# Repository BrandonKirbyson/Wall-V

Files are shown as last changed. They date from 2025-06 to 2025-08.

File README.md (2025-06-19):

# Wall-V (Wheeled and Legged Locomotion Vehicle)

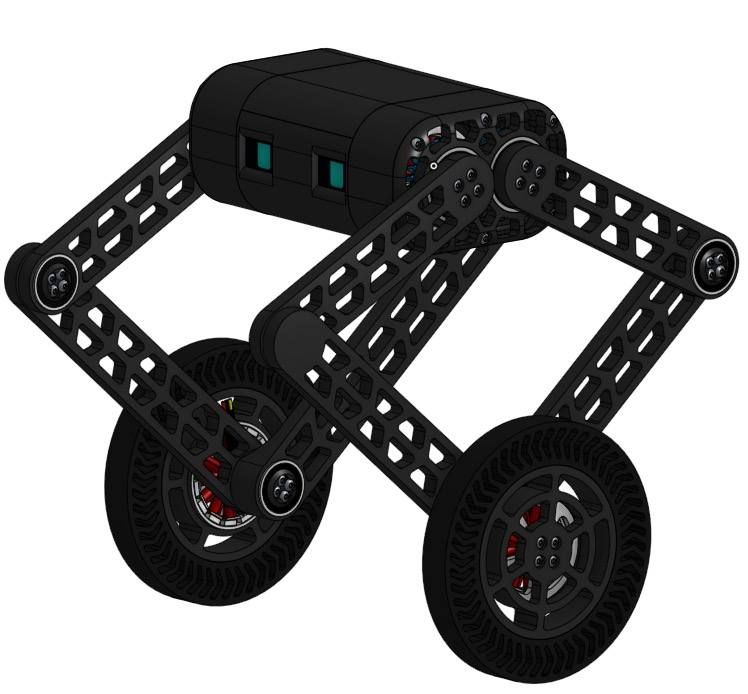
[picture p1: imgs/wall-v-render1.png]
Wall-V Render


Wall-V is a 2 legged, self-balancing robot that has wheels and can jump. It is designed to be able to go up hills and have uneven height on each side. The robot uses an ESP-Wroom-32 as a fast microcontroller to stay balanced. We are planning to use either PID to maintain balance.

## Why we are building this

We are building Wall-V to experiment with self-balacing robots that have the capability to jump. Jumping will allow to robot to go over small obstacles and be more manuverable and it will have to have high torque motors to align the robot.

So far throughout the building process, the hardest thing has been creating the leg design that allows the robot to jump. We have thought about many different designs but concluded that putting a ball bearing as the joint will still allow the robot to jump while not requiring an extra motor to move. The legs are both attached to each other and 1 motor will provide the torque to lift both legs at once. Additionally, the wheels are not linked so they can be at independent heights.

## Wiring Diagram

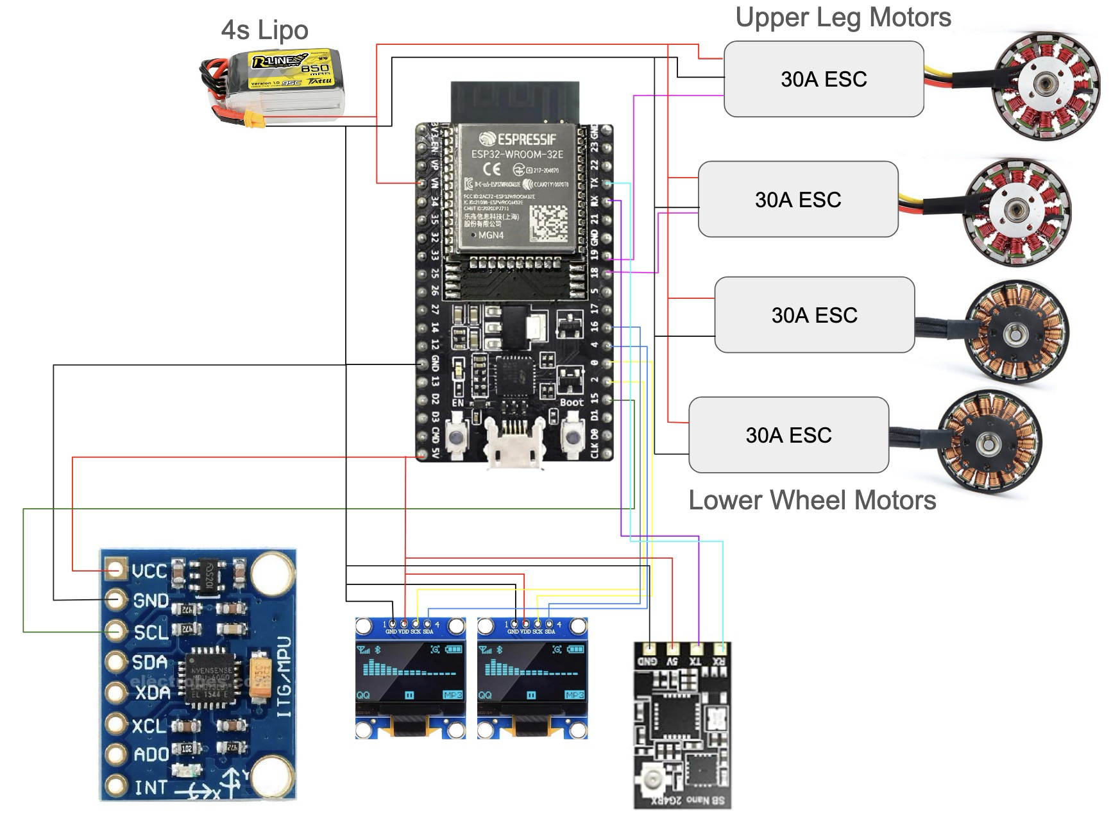
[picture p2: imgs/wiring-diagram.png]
Wiring Diagram


## Parts List

Subtotal Cost of Parts on Amazon: $123.9 (does not include tax and shipping)

Subtotal Cost of Parts on AliExpress: $34.89 (does not include tax and shipping)

Subtotal Cost of Parts: $158.79 (does not include tax and shipping)

Total Cost of Parts: $175.92 (includes tax and shipping)

Extra Spent on Amazon: $27.12 (extra we will cover for faster shipping, not spent using HCB funds)

| Quantity | Name | Notes | Amazon Link | Ali Link | Amazon Price | Aliexpress Price | Ordering From | Ordered |
| --- | --- | --- | --- | --- | --- | --- | --- | --- |
| 4 | VGEBY Brushless Motor 1PCS 5010 360KV | These two motors power the arms and have high torque that can quickly pull up the legs enabling the robot to jump | https://a.co/d/61lIr4G | https://www.aliexpress.us/item/2251832668557589.html | 27.62 | 15.10 | Aliexpress | 2/4 |
| 1 | WWZMDiB 4Pcs AS5600 Magnetic Encoder 3.3V 12bit high Precision Magnetic Induction Angle Measurement Sensor Module | These are used for getting motor position | https://a.co/d/6U3z8iJ | https://www.aliexpress.us/item/3256802834839452.html | 10.99 | 5.67 | Amazon | No |
| 1 | ESP32-DevKitC-32E Development Board | This is the main microcontroller for the robot which has a very fast tick rate for self-balancing | https://a.co/d/bIcHKEl | https://www.aliexpress.us/item/3256804290552594.html | 11 | 2.46 | Aliexpress | No |
| 4 | ZMR 40A Bidirectional Brushless 2-6S UBEC 3A 5V ESC | These ESCs will control the leg and wheel motors | https://a.co/d/9KbKRcA | https://www.aliexpress.us/item/2255800049335968.html | 14.99 | 11.89 | Amazon | No |
| 1 | MF148ZZ Flanged Ball Bearing ID 8mm x OD 14mm x Width 4mm | Smaller flanged bearings to support leg pivots | https://a.co/d/eTWzlf1 | https://www.aliexpress.us/item/3256807921303726.html | 8.99 | 5.49 | Amazon | No |
| 2 | F6802-2RS 10PCS Flanged Bearing 15×24×5mm | Medium size flanged bearings for the leg joints at knee and wheel | https://a.co/d/7eKafdc | (not cheaper) | 9.99 | - | Amazon | No |
| 1 | F6804-2RS 4PCS Flanged Ball Bearing 20mm x 32mm x 7mm | Larger flanged bearings for main leg pivot joints in the body | https://a.co/d/40CGgTH | (not cheaper) | 8.99 | - | Amazon | No |
| 1 | SpeedyBee ELRS FPV Receiver - 2.4ghz ExpressLRS Nano Receiver Drone RX Module with 78mm UFL T Antenna | ELRS receiver to control the robot with a remote | https://a.co/d/2ItnyXH | https://www.aliexpress.us/item/3256809002280211.html | 14.99 | 12.88 | Amazon | No |
| 1 | 0.96 Inch OLED Display Module 12864 LCD Screen 128x64 IIC I2C OLED Board SSD1315 | 2 small OLED screens that will serve as the robots eyes | https://a.co/d/b7wErMp | https://www.aliexpress.us/item/3256804169233174.html | 9.99 | 2.23 | Aliexpress | No |

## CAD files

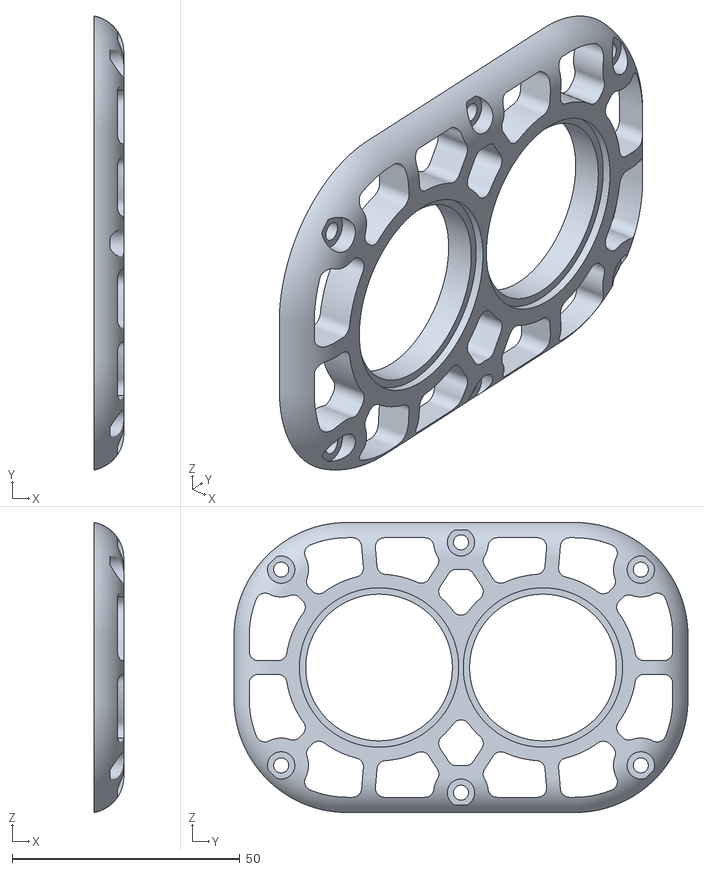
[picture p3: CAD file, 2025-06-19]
models/Leg Motor Cover.stl
6.50 x 99.7 x 63.7

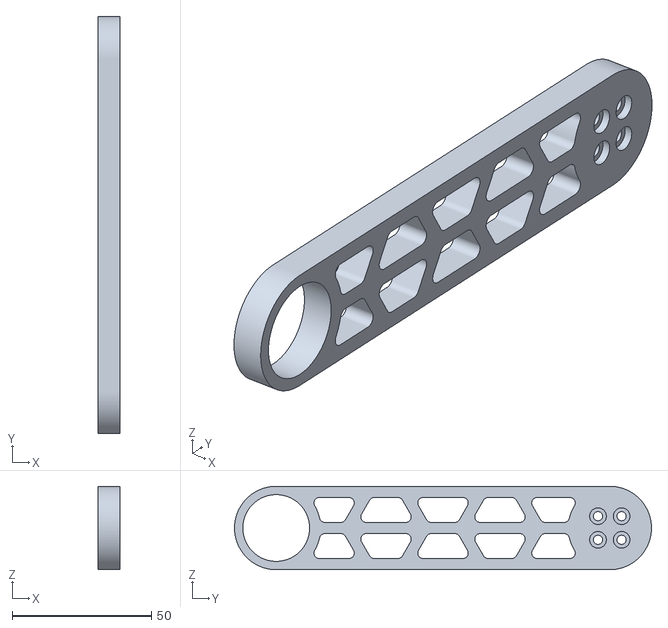
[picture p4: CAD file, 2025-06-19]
models/Front Upper Leg.stl
8.00 x 150.0 x 30.0

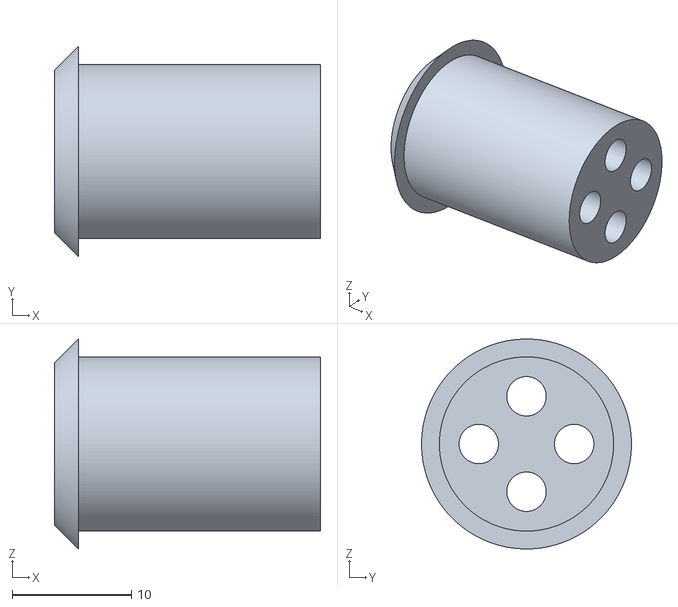
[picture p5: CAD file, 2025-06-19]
models/Wheel Joint Hub.stl
22.3 x 17.6 x 17.6

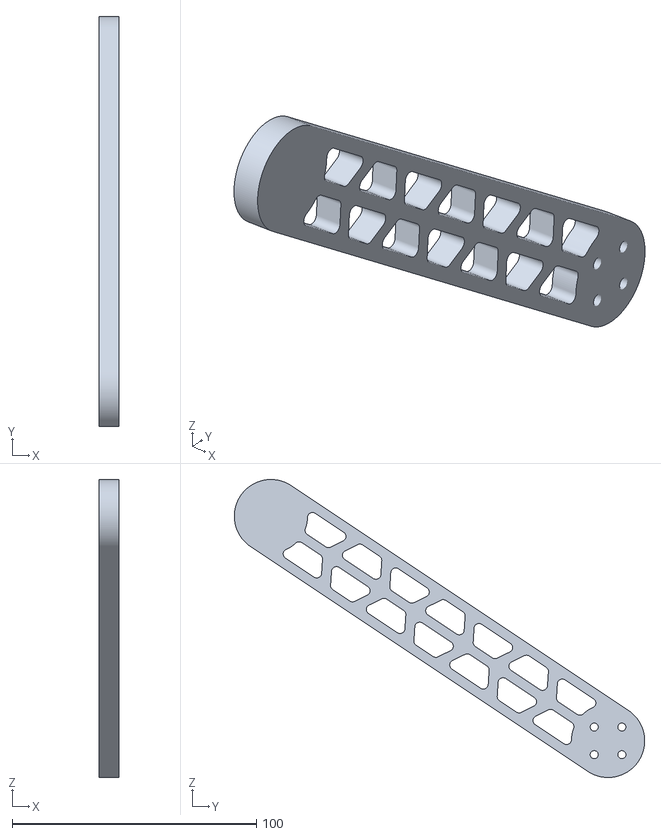
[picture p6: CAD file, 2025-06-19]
models/Front Lower Leg.stl
8.00 x 168.0 x 122.0

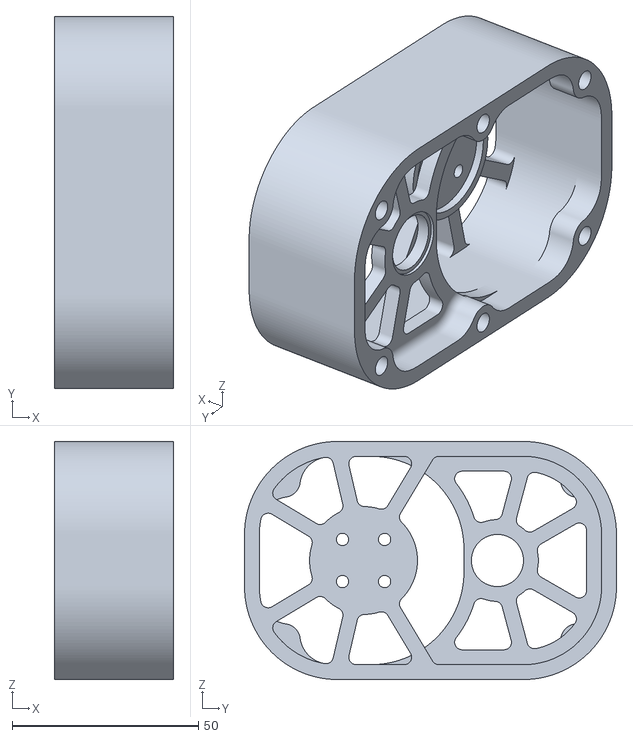
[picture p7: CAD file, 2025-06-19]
models/Right Motor Box.stl
32.0 x 100.0 x 64.0

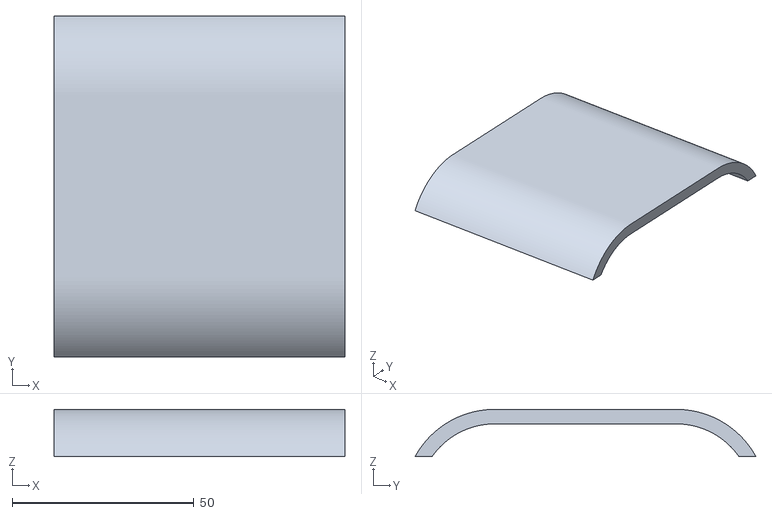
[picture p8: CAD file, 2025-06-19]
models/Upper Body.stl
80.0 x 93.9 x 13.0

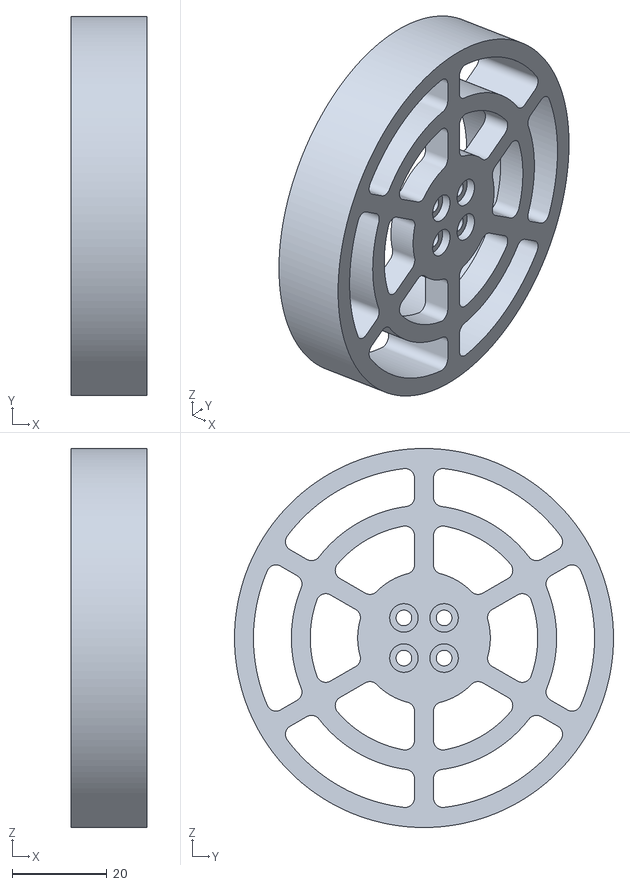
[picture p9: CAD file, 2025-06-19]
models/Wheel Hub.stl
16.0 x 80.0 x 80.0

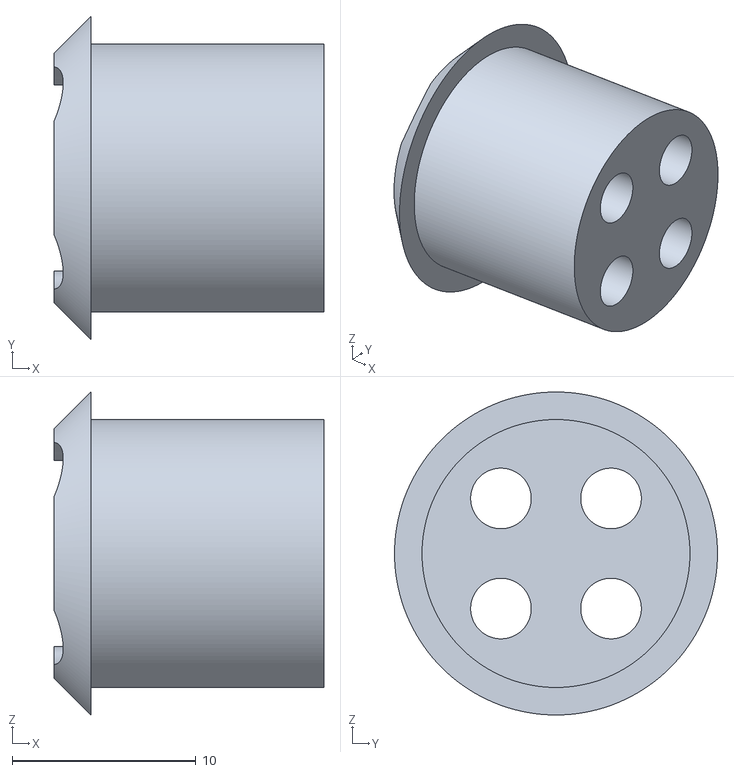
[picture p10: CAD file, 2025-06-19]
models/Knee Hub.stl
14.7 x 17.6 x 17.6

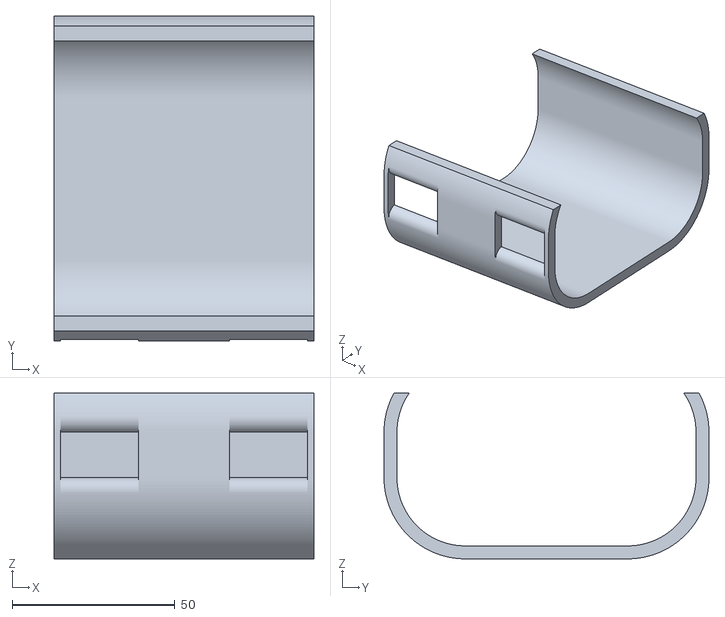
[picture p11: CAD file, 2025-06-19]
models/Lower Body.stl
80.0 x 100.0 x 51.0

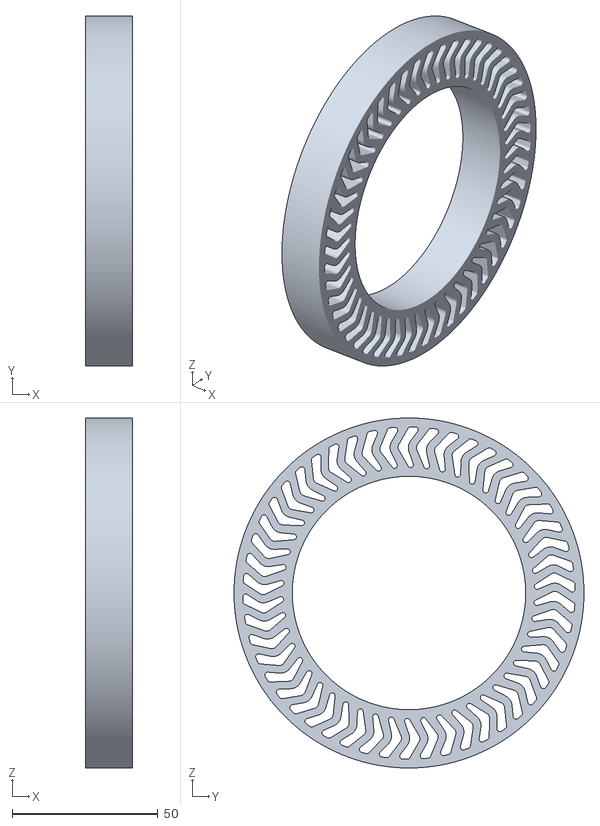
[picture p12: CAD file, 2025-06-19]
models/Tire (TPU).stl
16.0 x 120.0 x 120.0

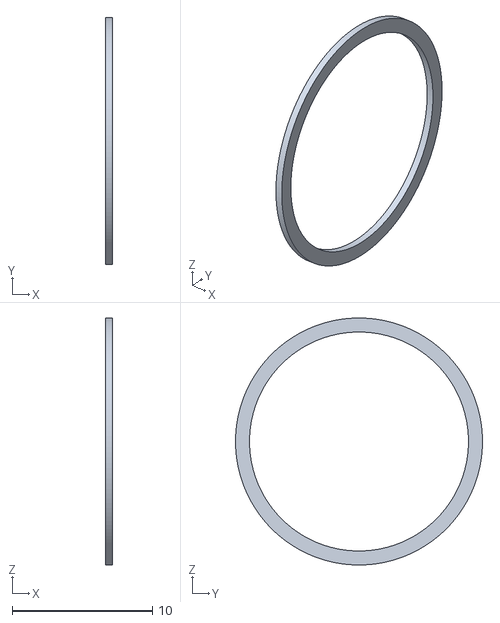
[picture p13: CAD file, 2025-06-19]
models/Knee Spacer.stl
0.5 x 17.6 x 17.6

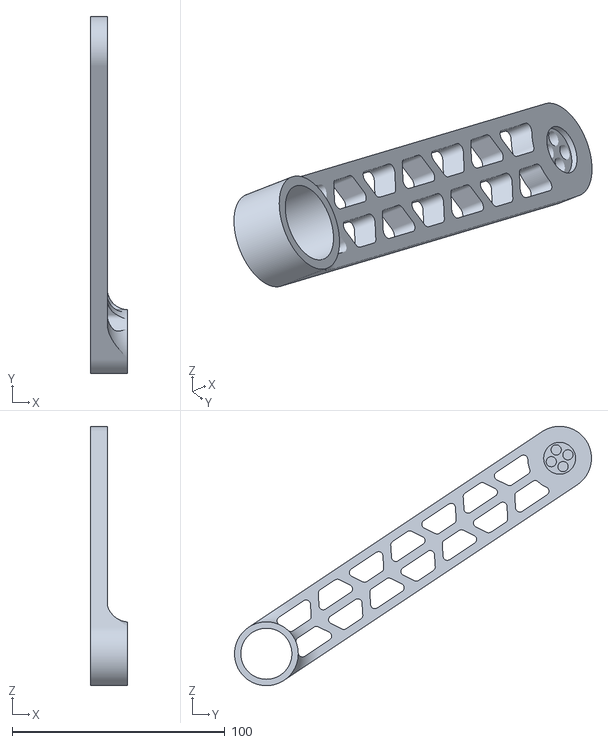
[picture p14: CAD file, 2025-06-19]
models/Back Lower Leg.stl
17.6 x 168.0 x 122.0

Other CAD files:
models/Right Motor Cover.stl
models/Back Upper Leg.stl
models/Leg Motor Box.stl

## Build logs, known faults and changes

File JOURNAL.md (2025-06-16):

---
title: "Wall-V"
author: "Brandon Kirbyson/Tobin Palmer"
description: "Wall-V is a 2 legged, self-balancing robot that has wheels and can jump."
created_at: "2025-06-10"
---

*Note for all time spent, it is counting for 1 person working on the bot, we both worked only worked on it together so the total time is listed here is half the amount for both of us*

## Total Time Spent: 13 Hours

## 6/11/25 - Initial Sketches and First CAD Design

### Time Spent: 2.5 Hours

We started by drawing an initial sketch of the robot's design. It has a motor and gear on each side which allow it to quickly move the wheels up to jump. Additionally, each side is independent so it can go up a hill and have uneven height on each side. We are planning to use an ESP-Wroom-32 as a fast microcontroller so the robot can stay balanced. We are planning to use PID or LQR to balance the robot.
Initial Sketch

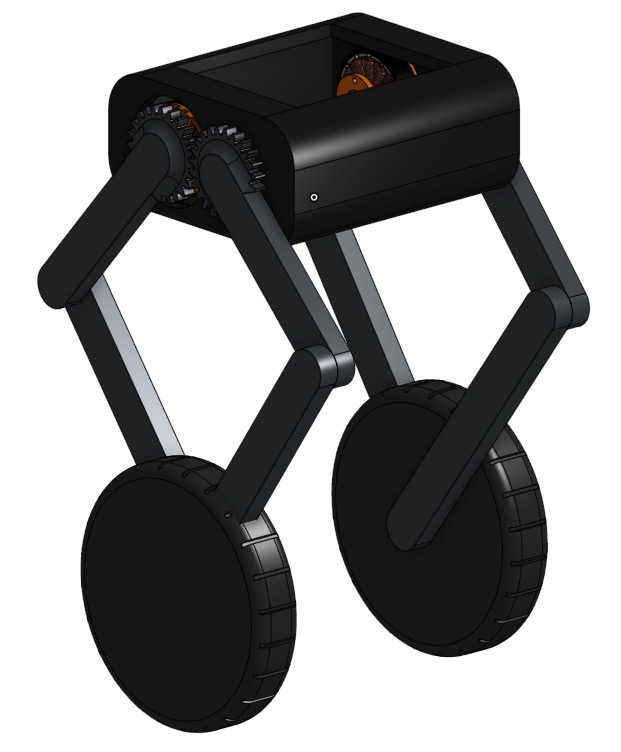
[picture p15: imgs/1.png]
Initial Robot Design


Initial CAD Design of the robot

## 6/12/25 - New CAD Design

### Time Spent: 3.5 Hours

We changed the CAD design to have a mount for the motor and also have the arms be properly mounted with a bearing. Additionally, we changed the style for the motor, now it has a 2 gear design that will ensure the wheels mainly stay centered under the bot.

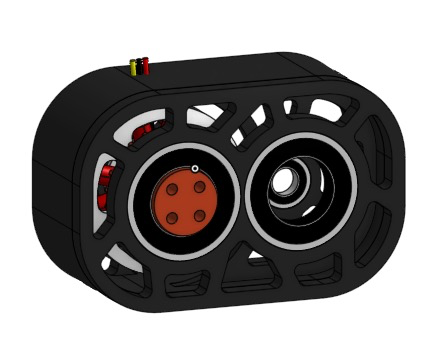
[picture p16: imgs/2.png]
Robot side with motor gears


View of motor without legs attached. Two bearings will help smoothly rotate each leg

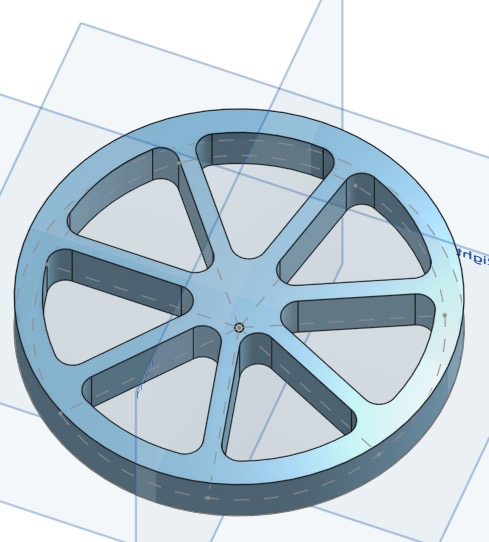
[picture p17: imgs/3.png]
Primative wheel design


Basic wheel which we will wrap rubber to give better traction.

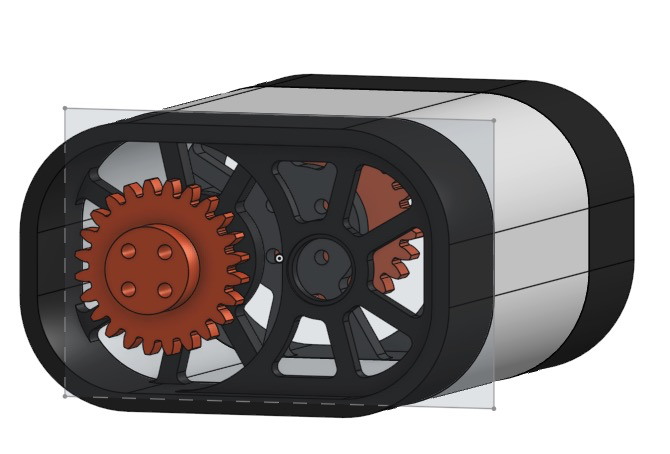
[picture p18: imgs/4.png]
Body of the robot with motors on either side


Joined halfs with empty space for battery, esc and microcontroller.

## 6/13/25 - CAD Design Nearly Finished

### Time Spent: 5 Hours

First picture of testing PID Proof of Concept

Second picture of testing PID Proof of Concept

While designing the model we started to test some old parts we had laying around to see if our IMU would work as fast enough to balance the robot. We used a servo as motor to see kindof what the code would look like, however, in our actual bot we would be using a brushless motor.

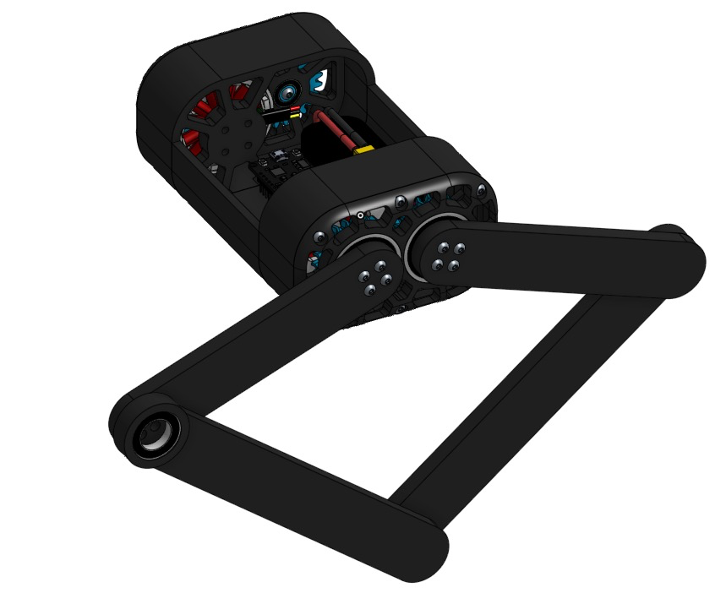
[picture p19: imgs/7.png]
Robot coming along


Picture of the robot with the motors and mounting fully done. We just need to add some mounting for the internal protoboard and fix the legs with proper bearings.

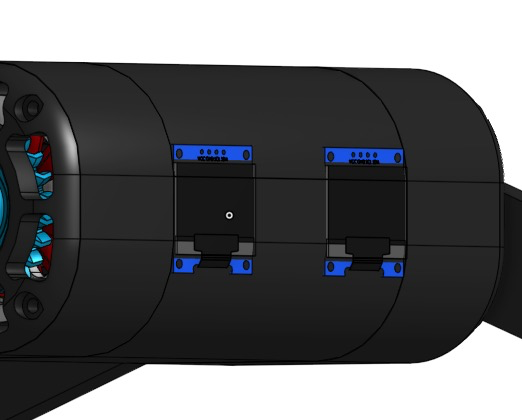
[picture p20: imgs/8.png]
The screens that will serve as eyes


These screens will be used as eyes and will ideally have a animation to might even be dependent on the speed of the robot. We are planning to use the ESP32 to control them.

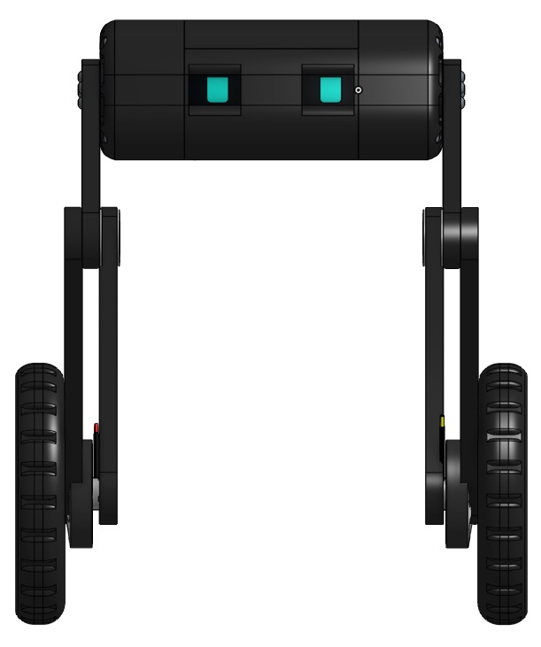
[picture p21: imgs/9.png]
Front view of Wall-V


The front view of the robot shows its design and how the wheels are mounted and an example face of the robot.

The only thing that needs to be improved is the legs and their mounting to the wheels.

## 6/14/25

### Time Spent: 2 Hours

Finished the CAD including making the leg joints work with a bearing and mounting the wheels onto the legs.

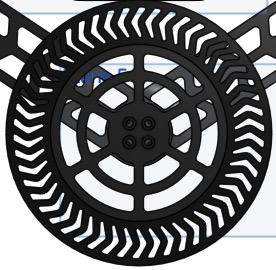
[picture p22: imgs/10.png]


The finished wheel design with a TPU tire to give it more traction. The wheel and leg are both designed to be very light so that the robot can quickly move its legs up and down without using an overly powerful motor.

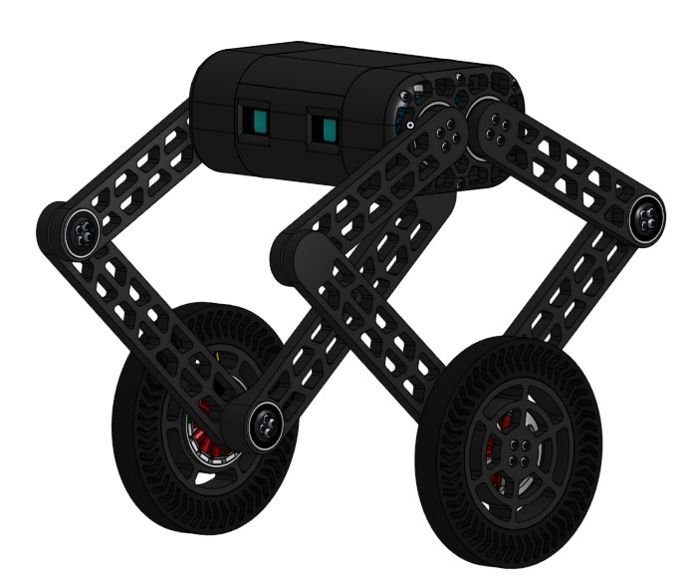
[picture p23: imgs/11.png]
Side view of the robot


The finished robot design

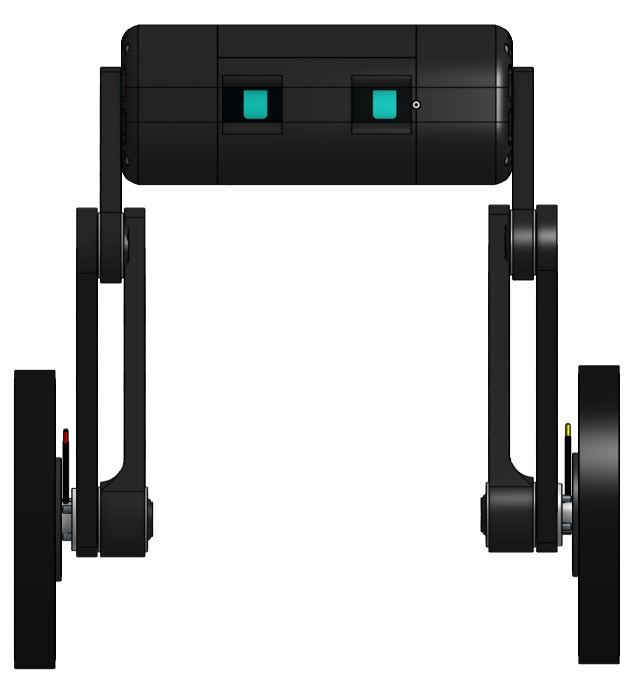
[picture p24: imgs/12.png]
Front view of the robot


Front view of the robot

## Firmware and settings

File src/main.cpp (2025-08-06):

#include <Arduino.h>

void setup()
{
  // Initialize serial communication at 9600 baud rate
  Serial.begin(9600);

  // Wait for the serial port to connect (useful for some boards)
  while (!Serial)
  {
    ; // Wait for serial port to connect. Needed for native USB port only
  }

  Serial.println("Hello, World!");
}

void loop()
{
  // Nothing to do here
  // The setup function already prints "Hello, World!" once
  delay(1000); // Optional: wait for a second before the next iteration
}

// #include <Arduino.h>
// #include <Wire.h>
// // #include <AS5600.h>
// #include <Servo.h>

// const int SW_pin = 2; // digital pin connected to switch output
// const int X_pin = 0;  // analog pin connected to X output
// const int Y_pin = 1;  // analog pin connected to Y output

// // AS5600 as5600;
// Servo esc;

// const int escPin = 12;

// // const float Kp = 0.5;
// // const float Ki = 0;
// // const float Kd = 0.1;
// // // const float Ki = 0.1;
// // // const float Kd = 0.5;

// // double targetAngle = 90.0;
// // double integral = 0.0;
// // double previousError = 0.0;
// // unsigned long lastTime = 0;

// double armExtendedPercent(int rawAngle);
// void setMotorPower(double percent);

// void setup()
// {
//   Serial.begin(9600);
//   Wire.begin();
//   esc.attach(escPin);
//   esc.writeMicroseconds(1000); // arm ESC

//   pinMode(SW_pin, INPUT);
//   digitalWrite(SW_pin, HIGH);

//   delay(2000);

//   // if (as5600.begin())
//   //   Serial.println("AS5600 Working");
//   // else
//   //   Serial.println("AS5600 Not working");

//   // lastTime = millis();
// }
// void loop()
// {
//   int yValue = analogRead(Y_pin);
//   Serial.print(" | Y: ");
//   Serial.println(yValue);

//   // convert Y value from 0-1020 to 0-100
//   double yPercent = (yValue / 1023.0) * 100.0;
//   Serial.print("Y Percent: ");
//   Serial.println(yPercent);

//   // int rawAngle = as5600.readAngle();
//   // double angle = armExtendedPercent(rawAngle);

//   // unsigned long now = millis();
//   // double dt = (now - lastTime) / 1000.0;
//   // lastTime = now;

//   // double error = targetAngle - angle;
//   // integral += error * dt;
//   // double derivative = (error - previousError) / dt;
//   // previousError = error;

//   // double output = Kp * error + Ki * integral + Kd * derivative;

//   // double motorPower = constrain(output, -100.0, 100.0);
//   setMotorPower(yPercent);

//   // // Debug output
//   // Serial.print("Angle: ");
//   // Serial.print(angle);
//   // Serial.print(" | Error: ");
//   // Serial.print(error);
//   // Serial.print(" | Output: ");
//   // Serial.println(output);

//   delay(3);
// }

// double armExtendedPercent(int rawAngle)
// {
//   const double MIN_ANGLE = 214;
//   const double MAX_ANGLE = 123;

//   const double MIN_POSITION = 0;
//   const double MAX_POSITION = 90;

//   double angle = rawAngle * 360.0 / 4096.0;

//   if (angle > MIN_ANGLE)
//     return MIN_POSITION;

//   return ((angle - MIN_ANGLE) * (MAX_POSITION - MIN_POSITION)) / (MAX_ANGLE - MIN_ANGLE);
// }

// void setMotorPower(double percent)
// {
//   percent = constrain(percent, -100.0, 100.0);

//   int pulseWidth = 1500 + (percent / 100.0) * 500.0;
//   esc.writeMicroseconds(pulseWidth);

//   Serial.print("Power set to ");
//   Serial.print(percent, 2);
//   Serial.print("% (");
//   Serial.print(pulseWidth);
//   Serial.println(" µs)");
// }

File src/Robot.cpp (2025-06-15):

#include "Robot.hpp"

Robot::Robot() : pid(1.0, 0.0, 0.05) {}

void Robot::begin()
{
    imu.begin();
    leftMotor.begin();
    rightMotor.begin();
}

void Robot::update(float dt)
{
    float angle = imu.getAngle();
    float correction = pid.compute(0.0, angle, dt);
    leftMotor.setSpeed(correction);
    rightMotor.setSpeed(correction);
}

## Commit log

2025-06-13 started BOM
    [BOM.csv]
2025-06-13 Updated BOM + journal
    [BOM.csv]
2025-06-14 updated journal and BOM
    [BOM.csv]
2025-06-14 Added wiring diagram and BOM to readme
2025-06-14 updated BOM + readme BOM
    [BOM.csv]
2025-06-15 Finished robot design'
    [BOM.csv]
2025-06-16 Changed to bi-directional ESP
    [BOM.csv]
2025-06-19 Added stl files to 3dp
    [Back Lower Leg.stl, Back Upper Leg.stl, Front Lower Leg.stl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]
2025-06-19 updated BOM
    [BOM.csv]
2025-06-19 Updated bom and totals
    [BOM.csv]
